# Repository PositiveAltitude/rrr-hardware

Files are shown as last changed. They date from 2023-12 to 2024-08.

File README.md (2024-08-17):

# RRR
This repo contains design files for experimental "RRR" flight computer for Thrust Vector Control model rockets. The main idea is to use an ESP32-C3 microcontroller (RISC V) and Rust programming language. So the name is Risc Rust Rocket.
Please keep in mind that this is a prototype and a proof of concept, so expect issues and design mistakes. All parts were sourced from LCSC, so you can find LCSC part numbers populated for every component.

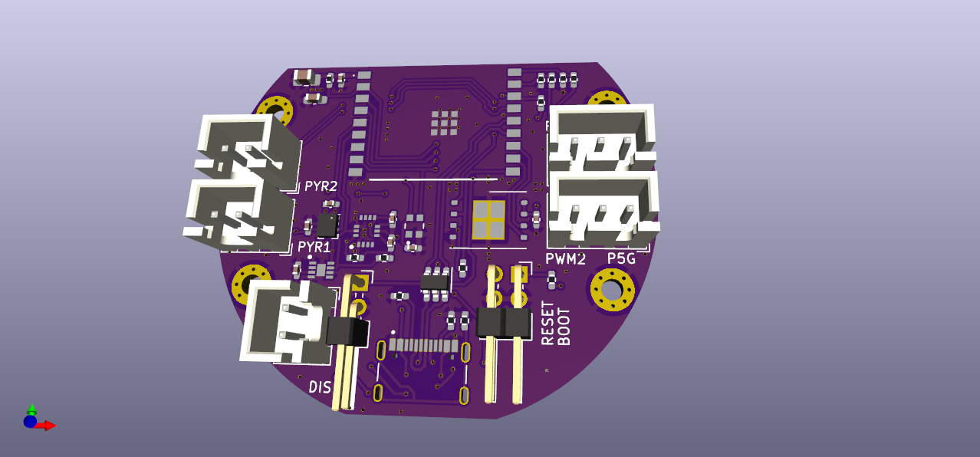
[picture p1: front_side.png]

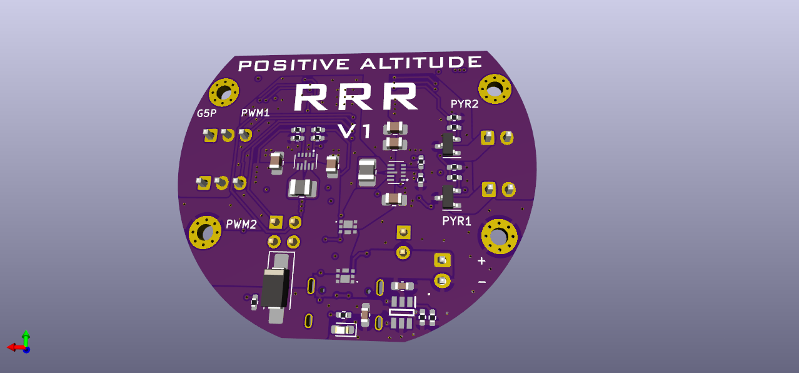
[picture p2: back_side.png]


### Know issues
- Inertia measurement unit Pin 12 (CSB) is wrongly connected to GND. It should be connected to VCC or floating. It is possible to fix this by carefully cutting two traces with a sharp knife under a microscope.
- Pyro channels transistors placed incorrectly. That could be fixed if you solder them rotated 120 degrees counter-clockwise. Looks quite ugly but possible.

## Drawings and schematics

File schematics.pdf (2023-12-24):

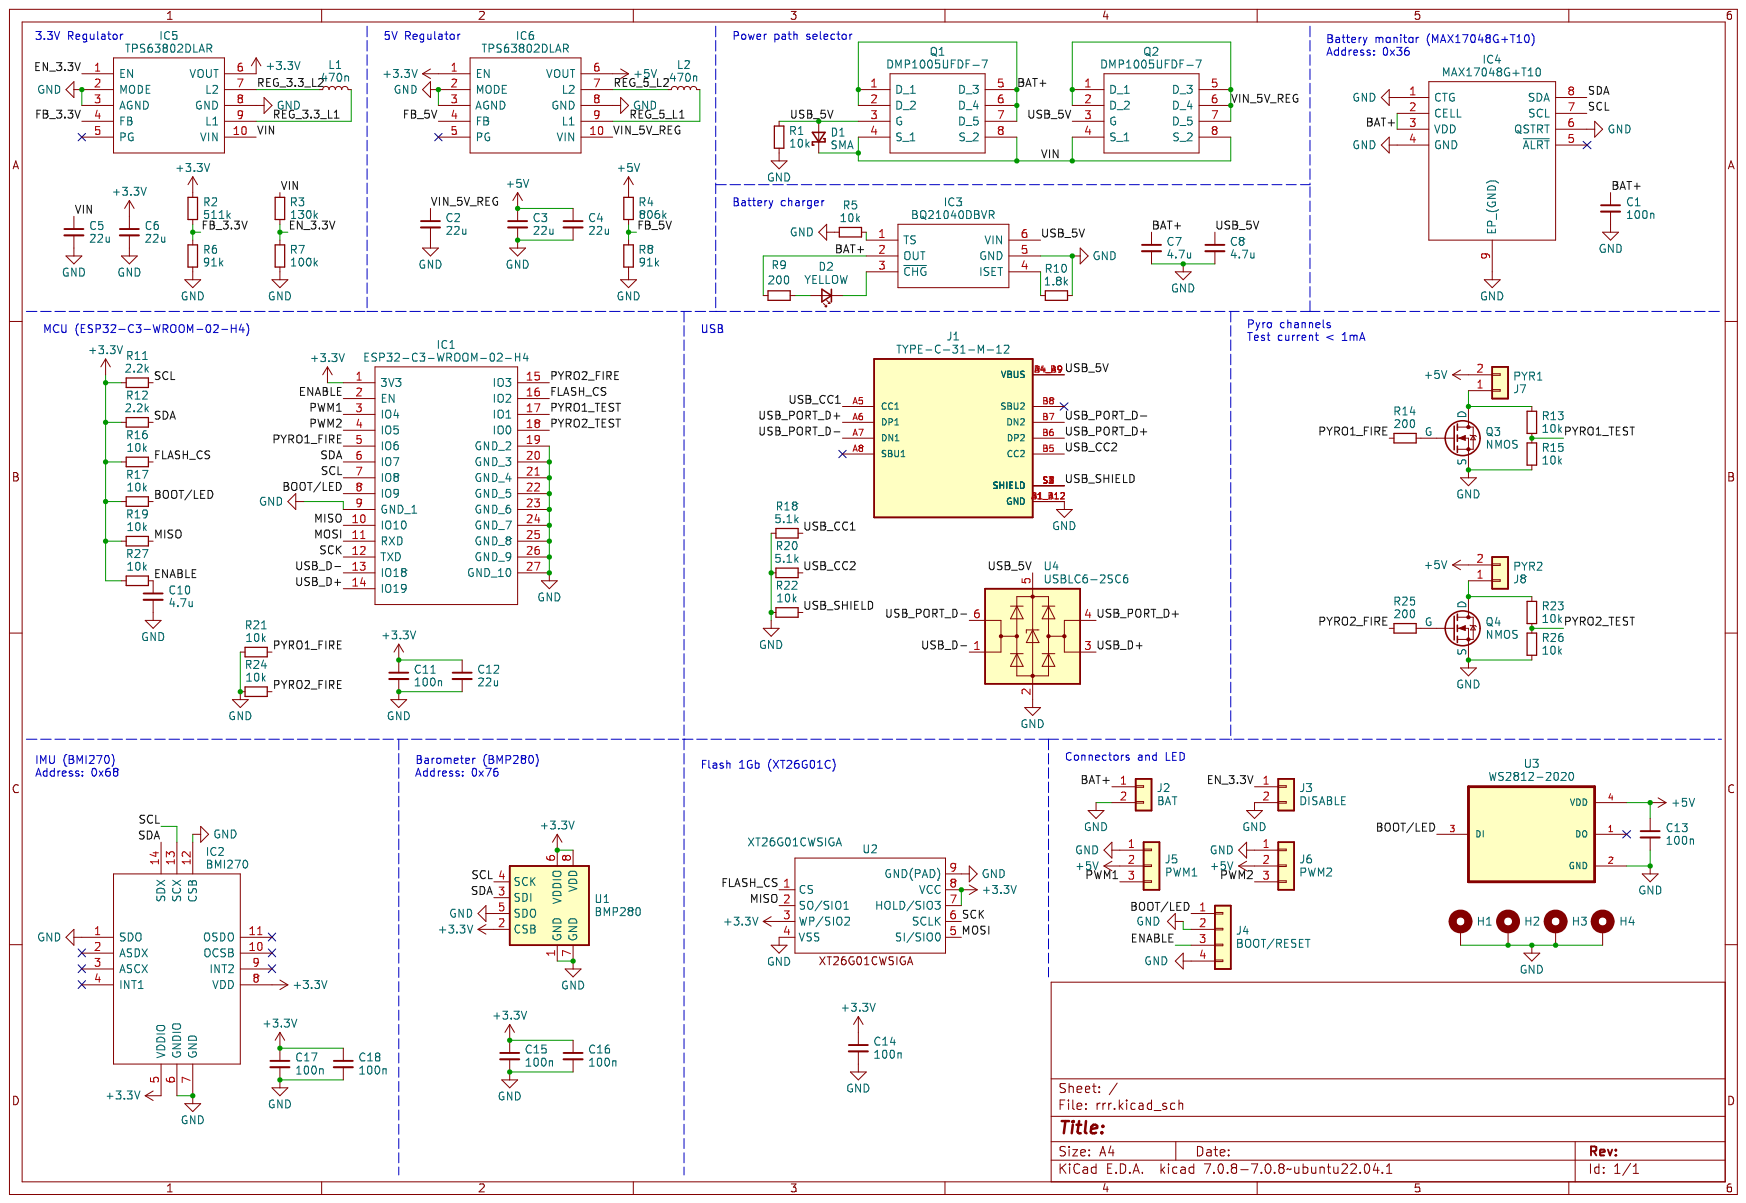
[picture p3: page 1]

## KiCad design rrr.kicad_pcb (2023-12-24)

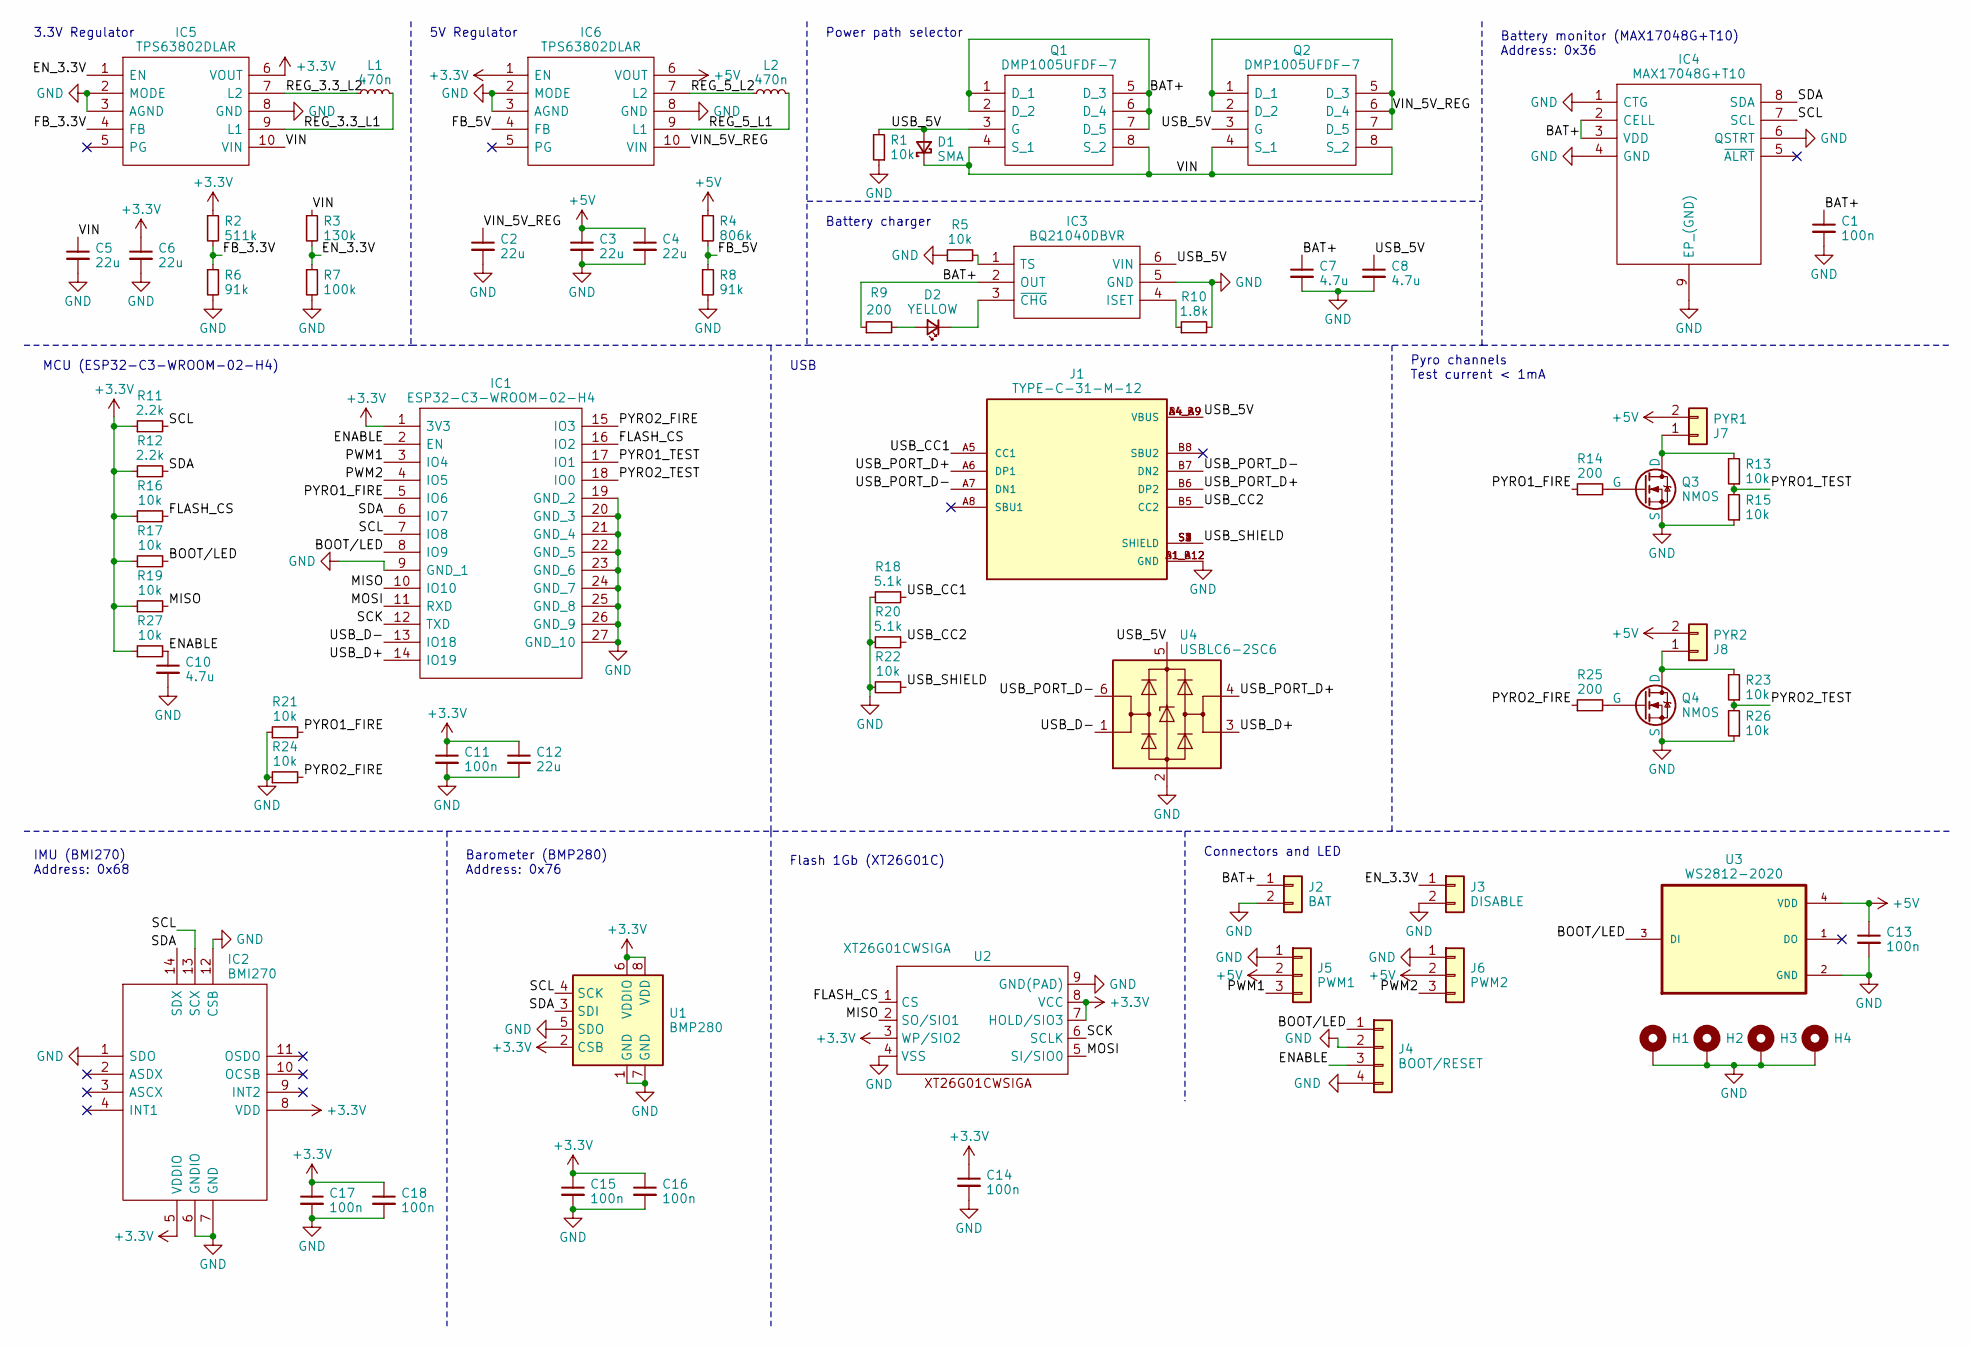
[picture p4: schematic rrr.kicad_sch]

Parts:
C1, C11, C13, C14, C15, C16, C17, C18: 100n; C_0402_1005Metric_Pad0.74x0.62mm_HandSolder; LCSC C85858
C2, C3, C4, C5, C6, C12: 22u; C_0805_2012Metric_Pad1.18x1.45mm_HandSolder; LCSC C86816
C7, C8, C10: 4.7u; C_0603_1608Metric_Pad1.08x0.95mm_HandSolder; LCSC C162274
D1: SMA; D_SMA_Handsoldering; LCSC C2983557
D2: YELLOW; LED_0603_1608Metric_Pad1.05x0.95mm_HandSolder; LCSC C72038
H1, H2, H3, H4: MountingHole_2.2mm_M2_Pad_Via
IC1: ESP32-C3-WROOM-02-H4; ESP32C3WROOM02H4; Mouser Part Number 356-ESP32C3WROOM02H4
IC2: BMI270; QFN50P300X250X87-14N; Mouser Part Number 262-BMI270
IC3: BQ21040DBVR; SOT95P280X145-6N; Mouser Part Number 595-BQ21040DBVR
IC4: MAX17048G+T10; SON50P200X200X80-9N-D; Mouser Part Number 700-MAX17048G+T10
IC5, IC6: TPS63802DLAR; Mouser Part Number 595-TPS63802DLAR
J1: TYPE-C-31-M-12; HRO_TYPE-C-31-M-12; PARTREV 2020.12.08; LCSC C165948
J2: BAT; JST_XH_B2B-XH-A_1x02_P2.50mm_Vertical; LCSC C158012
J3: DISABLE; PinHeader_2x01_P2.54mm_Horizontal; LCSC C492430
J4: BOOT/RESET; PinHeader_2x02_P2.54mm_Horizontal; LCSC C492430
J5: PWM1; JST_XH_B3B-XH-A_1x03_P2.50mm_Vertical; LCSC C144394
J6: PWM2; JST_XH_B3B-XH-A_1x03_P2.50mm_Vertical; LCSC C144394
J7: PYR1; JST_XH_B2B-XH-A_1x02_P2.50mm_Vertical; LCSC C158012
J8: PYR2; JST_XH_B2B-XH-A_1x02_P2.50mm_Vertical; LCSC C158012
L1, L2: 470n; L_1008_2520Metric_Pad1.43x2.20mm_HandSolder; LCSC C1333867
Q1, Q2: DMP1005UFDF-7; DMP1005UFDF7; Mouser Part Number 621-DMP1005UFDF-7
Q3, Q4: NMOS; SOT-23; LCSC C3280164
R1, R5, R13, R15, R16, R17, R19, R21, R22, R23, R24, R26, R27: 10k; R_0402_1005Metric_Pad0.72x0.64mm_HandSolder; LCSC C60490
R2: 511k; R_0402_1005Metric_Pad0.72x0.64mm_HandSolder; LCSC C163461
R3: 130k; R_0402_1005Metric_Pad0.72x0.64mm_HandSolder; LCSC C93946
R4: 806k; R_0402_1005Metric_Pad0.72x0.64mm_HandSolder; LCSC C3016043
R6, R8: 91k; R_0402_1005Metric_Pad0.72x0.64mm_HandSolder; LCSC C327323
R7: 100k; R_0402_1005Metric_Pad0.72x0.64mm_HandSolder; LCSC C60491
R9, R14, R25: 200; R_0402_1005Metric_Pad0.72x0.64mm_HandSolder; LCSC C114764
R10: 1.8k; R_0402_1005Metric_Pad0.72x0.64mm_HandSolder; LCSC C163481
R11, R12: 2.2k; R_0402_1005Metric_Pad0.72x0.64mm_HandSolder; LCSC C114762
R18, R20: 5.1k; R_0402_1005Metric_Pad0.72x0.64mm_HandSolder; LCSC C105872
U1: BMP280; Bosch_LGA-8_2x2.5mm_P0.65mm_ClockwisePinNumbering; LCSC C83291
U2: XT26G01CWSIGA; WSON-8-1EP_8x6mm_P1.27mm_EP3.4x4.3mm; LCSC C2833378
U3: WS2812-2020; LED_WS2812-2020; PARTREV V1.3; LCSC C965555
U4: USBLC6-2SC6; SOT-23-6; LCSC C7519

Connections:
+3.3V: C6.1, C11.1, C12.1, C14.1, C15.1, C16.1, C17.1, C18.1, IC1.1 (3V3), IC2.5 (VDDIO), IC2.8 (VDD), IC5.6 (VOUT), IC6.1 (EN), R2.1, R11.1, R12.1, R16.1, R17.1, R19.1, R27.1, U1.2 (CSB), U1.6 (VDDIO), U1.8 (VDD), U2.3 (WP/SIO2), U2.7 (HOLD/SIO3), U2.8 (VCC)
+5V: C3.1, C4.1, C13.1, IC6.6 (VOUT), J5.2, J6.2, J7.2, J8.2, R4.1, U3.4 (VDD)
/BAT+: C1.1, C7.1, IC3.2 (OUT), IC4.2 (CELL), IC4.3 (VDD), J2.1, Q1.1 (D_1), Q1.2 (D_2), Q1.5 (D_3), Q1.6 (D_4), Q1.7 (D_5), R9.1
/BOOT/LED: IC1.8 (IO9), J4.1, R17.2, U3.3 (DI)
/ENABLE: C10.1, IC1.2 (EN), J4.3, R27.2
/EN_3.3V: IC5.1 (EN), J3.1, R3.2, R7.1
/FB_3.3V: IC5.4 (FB), R2.2, R6.1
/FB_5V: IC6.4 (FB), R4.2, R8.1
/FLASH_CS: IC1.16 (IO2), R16.2, U2.1 (CS)
/MISO: IC1.10 (IO10), R19.2, U2.2 (SO/SIO1)
/MOSI: IC1.11 (RXD), U2.5 (SI/SIO0)
/PWM1: IC1.3 (IO4), J5.3
/PWM2: IC1.4 (IO5), J6.3
/PYRO1_FIRE: IC1.5 (IO6), R14.1, R21.2
/PYRO1_TEST: IC1.17 (IO1), R13.1, R15.2
/PYRO2_FIRE: IC1.15 (IO3), R24.2, R25.1
/PYRO2_TEST: IC1.18 (IO0), R23.1, R26.2
/REG_3.3_L1: IC5.9 (L1), L1.2
/REG_3.3_L2: IC5.7 (L2), L1.1
/REG_5_L1: IC6.9 (L1), L2.2
/REG_5_L2: IC6.7 (L2), L2.1
/SCK: IC1.12 (TXD), U2.6 (SCLK)
/SCL: IC1.7 (IO8), IC2.13 (SCX), IC4.7 (SCL), R11.2, U1.4 (SCK)
/SDA: IC1.6 (IO7), IC2.14 (SDX), IC4.8 (SDA), R12.2, U1.3 (SDI)
/USB_5V: C8.1, D1.2 (A), IC3.6 (VIN), J1.A4_B9 (VBUS), J1.B4_A9 (VBUS), Q1.3 (G), Q2.3 (G), R1.2, U4.5 (VBUS)
/USB_CC1: J1.A5 (CC1), R18.1
/USB_CC2: J1.B5 (CC2), R20.1
/USB_D+: IC1.14 (IO19), U4.3 (I/O2)
/USB_D-: IC1.13 (IO18), U4.1 (I/O1)
/USB_PORT_D+: J1.A6 (DP1), J1.B6 (DP2), U4.4 (I/O2)
/USB_PORT_D-: J1.A7 (DN1), J1.B7 (DN2), U4.6 (I/O1)
/USB_SHIELD: J1.S1 (SHIELD), J1.S2 (SHIELD), J1.S3 (SHIELD), J1.S4 (SHIELD), R22.1
/VIN: C5.1, D1.1 (K), IC5.10 (VIN), Q1.4 (S_1), Q1.8 (S_2), Q2.4 (S_1), Q2.8 (S_2), R3.1
/VIN_5V_REG: C2.1, IC6.10 (VIN), Q2.1 (D_1), Q2.2 (D_2), Q2.5 (D_3), Q2.6 (D_4), Q2.7 (D_5)
GND: C1.2, C2.2, C3.2, C4.2, C5.2, C6.2, C7.2, C8.2, C10.2, C11.2, C12.2, C13.2, C14.2, C15.2, C16.2, C17.2, C18.2, H1.1, H2.1, H3.1, H4.1, IC1.9 (GND_1), IC1.19 (GND_2), IC1.20 (GND_3), IC1.21 (GND_4), IC1.22 (GND_5), IC1.23 (GND_6), IC1.24 (GND_7), IC1.25 (GND_8), IC1.26 (GND_9), IC1.27 (GND_10), IC2.1 (SDO), IC2.6 (GNDIO), IC2.7 (GND), IC2.12 (CSB), IC3.5 (GND), IC4.1 (CTG), IC4.4 (GND), IC4.6 (QSTRT), IC4.9 (EP_(GND)), IC5.2 (MODE), IC5.3 (AGND), IC5.8 (GND), IC6.2 (MODE), IC6.3 (AGND), IC6.8 (GND), J1.A1_B12 (GND), J1.B1_A12 (GND), J2.2, J3.2, J4.2, J4.4, J5.1, J6.1, Q3.3 (S), Q4.3 (S), R1.1, R5.1, R6.2, R7.2, R8.2, R10.2, R15.1, R18.2, R20.2, R21.1, R22.2, R24.1, R26.1, U1.1 (GND), U1.5 (SDO), U1.7 (GND), U2.4 (VSS), U2.9 (GND(PAD)), U3.2 (GND), U4.2 (GND)
unnamed: D2.2 (A), R9.2
unnamed: D2.1 (K), IC3.3 (~CHG)
unnamed: IC3.4 (ISET), R10.1
unnamed: IC3.1 (TS), R5.2
unnamed: J7.1, Q3.1 (D), R13.2
unnamed: J8.1, Q4.1 (D), R23.2
unnamed: Q3.2 (G), R14.2
unnamed: Q4.2 (G), R25.2

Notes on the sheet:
Connectors and LED
IMU (BMI270) Address: 0x68
Flash 1Gb (XT26G01C)
3.3V Regulator
USB
Barometer (BMP280) Address: 0x76
5V Regulator
Pyro channels Test current < 1mA
Battery monitor (MAX17048G+T10) Address: 0x36
MCU (ESP32-C3-WROOM-02-H4)
Battery charger
Power path selector

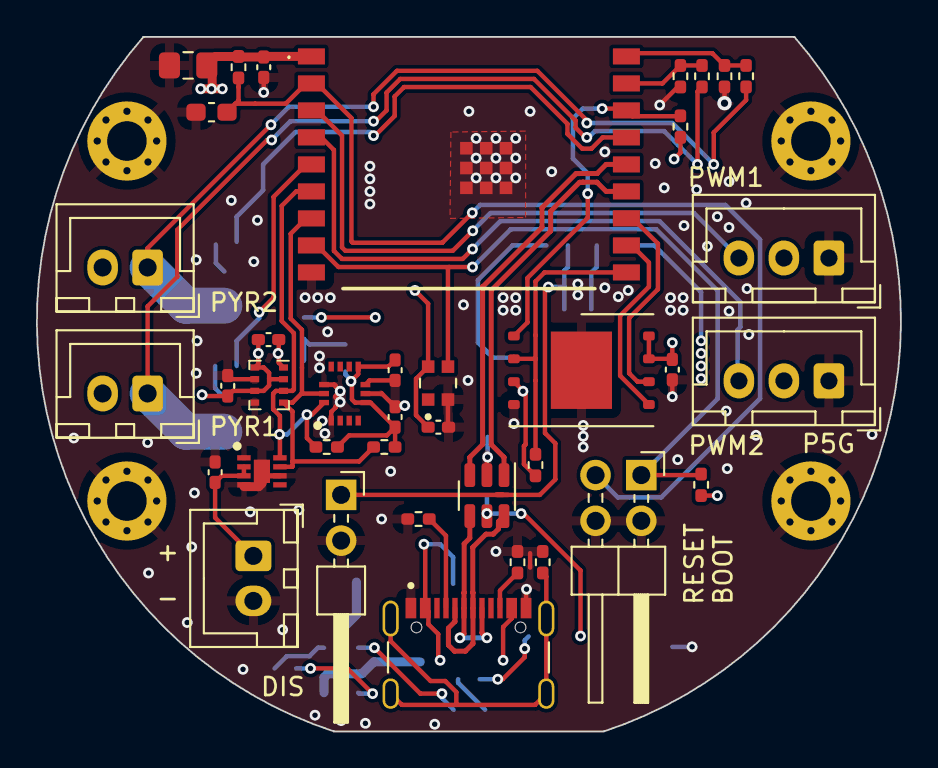
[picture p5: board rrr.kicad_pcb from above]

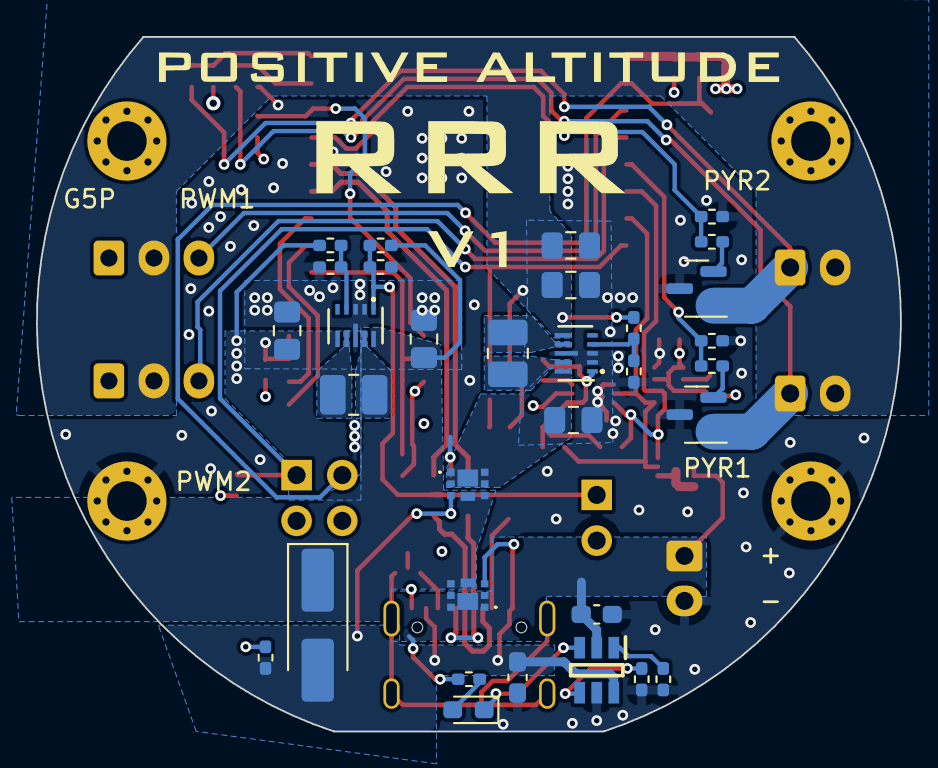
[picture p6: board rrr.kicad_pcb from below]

Board: 4 copper layers, 48.0 x 38.6 mm, 74 parts (32 on the bottom side), 43 nets.
